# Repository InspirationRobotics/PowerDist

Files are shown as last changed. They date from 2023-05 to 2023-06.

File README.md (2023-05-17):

# PowerDist

`kicad` holds the kicad project / gerber files for the board, and `Power_dist` holds the code running on the microcontroller that actually does the 
hot-swapping.

The [BOM](https://docs.google.com/spreadsheets/d/1eEv6u52QYOC_kODey6bpNA8GYwr_zVqGhBdzeqPN1tI/edit?usp=sharing) holds all the internal component references 
that are in the kicad project i.e. component '1,1' is a 102k 0603 resistor. 

The [datasheet](https://docs.google.com/document/d/1oroizqdIsIZM1mA43HTIwGpKUFsHDlDQZaLfoY1nW0c/edit) for the board holds some useful information about the 
board capabilities and issues.

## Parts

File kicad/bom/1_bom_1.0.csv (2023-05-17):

Component | Description | Part | References | Value | Footprint | Quantity Per PCB | Datasheet | PN | Arrow Part Number | Arrow Price/Stock | Height | Manufacturer_Name | Manufacturer_Part_Number | Mouser Part Number | Mouser Price/Stock | Link
1 | Unpolarized capacitor | C | C3 C7 C29 C30 | 0.1uF | C_1608_603_B | 4 | ~
2 | Unpolarized capacitor | C | C2 C4 C8 | 1uF | C_1608_603_B | 3 | ~
3 | Unpolarized capacitor | C | C1 C14 C15 C16 C20 C21 C22 C26 C27 C28 | 10uF | C_1608_603_B | 10 | ~ | 100,000,013
4 | Unpolarized capacitor | C | C11 C12 C13 C17 C18 C19 C23 C24 C25 | 10uF | C_2012_805_B | 9 | ~ | 100,000,013
5 | Polarized capacitor | CP | C5 C6 C9 C10 | 470uF | THT_470uF_Cap | 4 | https://api.kemet.com/component-edge/download/datasheet/ESK477M025AH1AA.pdf
6 | Schottky diode | D_Schottky | D1 D2 | D_Schottky | D_SOD-323 | 2 | ~
7 | Light emitting diode | LED | D3 D4 D5 D6 D7 D8 D9 D10 | LED | R_1608_603_B | 8 | ~
8 | ARM Microcontrollers - MCU 256KB 32KB 48QFN GRN1.6-3.6V48MHz | ATSAMD21G18A-MUT | IC2 | ATSAMD21G18A-MUT | QFN50P700X700X90-49N-D | 1 | https://datasheet.datasheetarchive.com/originals/distributors/DKDS41/DSANUWW0026743.pdf |  | ATSAMD21G18A-MUT | https://www.arrow.com/en/products/atsamd21g18a-mut/microchip-technology?region=nac | 0.9 | Microchip | ATSAMD21G18A-MUT | 556-ATSAMD21G18A-MUT | https://www.mouser.co.uk/ProductDetail/Microchip-Technology-Atmel/ATSAMD21G18A-MUT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
9 |  | GD25Q16CWIGR | IC1 | GD25Q16CWIGR | PSON50P200X300X50-9N | 1 | https://ms.componentsearchengine.com/Datasheets/1/GD25Q16CWIGR.pdf |  |  |  | 0.8 | GigaDevice | GD25Q16CWIGR | 363-GD25Q16CWIGR | https://www.mouser.co.uk/ProductDetail/GigaDevice/GD25Q16CWIGR?qs=RcG8xmE7yp1dgxRTSLG3FQ%3D%3D
10 | USB Type A connector | USB_A | J2 | USB_A | amphenol_micro_usb_no_flange_10118192 | 1
11 |  | header_01x04 | J5 J6 | header_01x04 | Stemma_QT_2 | 2
12 |  | header_01x05 | J1 | header_01x05 | header_01x05_pitch2.54_tht | 1
13 | uSD Card connector | uSDCard | J7 | uSDCard | uSDCard_SD_503182_011 | 1 | x-devonthink-item://89382DC3-A8BA-4AFE-B050-E9E1112677D4
14 | Net tie, 4 pins | Net-Tie_4 | NT1 | Net-Tie_4 | NetTie-4_SMD_Pad2.0mm | 1 | ~
15 |  | CONN_1 | P1 P2 | CONN_1 | header_01x01_tht | 2
16 | NPN transistor, base/emitter/collector | BC847 | Q1 Q2 Q4 Q8 | BC847 | SOT-23 | 4 | ~ | 400,000,003
17 | N-MOSFET transistor, source/gate/drain | Q_NMOS_SGD | Q3 Q5 | PMOS_SGD | VDFN-8 | 2 | https://www.ti.com/lit/ds/symlink/csd25404q3.pdf?HQS=dis-dk-null-digikeymode-dsf-pf-null-wwe&ts=1673399419393
18 | Resistor | R | R38 R39 R40 R41 R42 R43 R44 R45 R46 R47 | 300 | R_1608_603_B | 10 | ~
19 | Resistor | R | R5 R9 R15 R16 | 470 | R_1608_603_B | 4 | ~
20 | Resistor | R | R8 R11 R22 R24 R51 R52 | 500 | R_2012_805_B | 6 | ~
21 | Resistor | R | R3 R4 R12 R13 R25 R26 R50 | 1k | R_1608_603_B | 7 | ~
22 | Resistor | R | R7 R10 R18 R20 R21 R23 | 4k7 | R_1608_603_B | 6 | ~
23 | Resistor | R | R1 R2 R6 R14 R48 R49 R53 | 10k | R_1608_603_B | 7 | ~ | 200,000,004
24 | Resistor | R | R17 R19 | 22k | R_1608_603_B | 2 | ~
25 | Resistor | R | R33 R35 R37 | 32.4k | R_1608_603_B | 3 | ~
26 | Resistor | R | R29 R30 R31 | 75k | R_1608_603_B | 3 | ~
27 | Resistor | R | R32 R34 R36 | 102k | R_1608_603_B | 3 | ~
28 |  | buzzer | SP1 SP2 | buzzer | 13-9mm_Buzzer | 2
29 | Push button switch, generic, two pins | SW_Push | SW1 | SW_Push | CK_PTS645_SMD | 1
30 |  | ACS781_1 | U2 U3 | ACS781 | 7-LR-PSOF | 2
31 |  | ARM-SWD-10 | U1 | ARM-SWD-10 | ARM-SWD-10 | 1 | http://suddendocs.samtec.com/catalog_english/ftsh_smt.pdf |  |  |  |  |  |  |  |  | https://www.digikey.com/en/products/detail/samtec-inc/FTSH-105-01-L-DV-K/1875039
32 |  | LM1085_2 | U10 U11 U12 | LM1085-3.0 | TO-263-3_TabPin2 | 3 | https://www.ti.com/general/docs/suppproductinfo.tsp?distId=10
33 |  | LM1085_1 | U7 U8 U9 | LM1085-5.0 | TO-263-3_TabPin2 | 3 | https://www.ti.com/lit/ds/symlink/lm1085.pdf?HQS=dis-dk-null-digikeymode-dsf-pf-null-wwe&ts=1674503286246
34 |  | MPM3610_1 | U4 U5 U6 | MPM3610 | 20-PowerLQFN | 3
35 |  | PCT2075 | U13 U14 | PCT2075 | PCT2075TP_147 | 2
36 |  | XT90PW-M | U15 U16 | XT90PW-M | AMASS_XT90PW-M_Horizontal | 2
37 |  | XT90PW-M | U17 U18 U19 U20 U21 U22 | XT90PW-M | AMASS_XT30U-F_1x02_P5.0mm_Vertical | 6
38 |  | XT90PW-M | U23 U24 U25 | XT90PW-M | AMASS_XT60-F_1x02_P7.20mm_Vertical | 3
Component Groups: | 38
Component Count: | 135
Fitted Components: | 135
Number of PCBs: | 1
Total components: | 135
Schematic Version: | 1.0
Schematic Date: | 2023-01-11
PCB Variant: | default
BoM Date: | Friday, January 27, 2023 at 11:06:49 AM
Schematic Source: | 1.0.kicad_sch
KiCad Version: | Eeschema (6.0.10-0)

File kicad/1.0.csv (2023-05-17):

Source: | /Users/seanboerhout/Documents/KiCAD/6.0/projects/Inspiration/Power_Dist/1.0/1.0.kicad_sch
Date: | Monday, January 23, 2023 at 03:24:27 PM
Tool: | Eeschema (6.0.10-0)
Generator: | /Applications/KiCad/KiCad.app/Contents/SharedSupport/plugins/bom_csv_grouped_by_value.py
Component Count: | 127
Individual Components:
Item | Qty | Reference(s) | Value | LibPart | Footprint | Datasheet | Arrow Part Number | Arrow Price/Stock | Description | Height | Link | Manufacturer_Name | Manufacturer_Part_Number | Mouser Part Number | Mouser Price/Stock | PN | Part
 |  | C1 | 10uF | 2.passive:C | 2_Passives_Capacitors_SMD_IPC:C_1608_603_B | ~ |  |  |  |  |  |  |  |  |  | 100,000,013
 |  | C2 | 1uF | 2.passive:C | 2_Passives_Capacitors_SMD_IPC:C_1608_603_B | ~ |  |  |  |  |  |  |  |  |  |  | 0603YC105KAT2A
 |  | C3 | 0.1uF | 2.passive:C | 2_Passives_Capacitors_SMD_IPC:C_1608_603_B | ~
 |  | C4 | 1uF | 2.passive:C | 2_Passives_Capacitors_SMD_IPC:C_1608_603_B | ~
 |  | C5 | 470uF | 2.passive:CP | 0_misc:THT_470uF_Cap | https://api.kemet.com/component-edge/download/datasheet/ESK477M025AH1AA.pdf
 |  | C6 | 470uF | 2.passive:CP | 0_misc:THT_470uF_Cap | https://api.kemet.com/component-edge/download/datasheet/ESK477M025AH1AA.pdf
 |  | C7 | 0.1uF | 2.passive:C | 2_Passives_Capacitors_SMD_IPC:C_1608_603_B | ~
 |  | C8 | 1uF | 2.passive:C | 2_Passives_Capacitors_SMD_IPC:C_1608_603_B | ~
 |  | C9 | 470uF | 2.passive:CP | 0_misc:THT_470uF_Cap | https://api.kemet.com/component-edge/download/datasheet/ESK477M025AH1AA.pdf
 |  | C10 | 470uF | 2.passive:CP | 0_misc:THT_470uF_Cap | https://api.kemet.com/component-edge/download/datasheet/ESK477M025AH1AA.pdf
 |  | C11 | 10uF | 2.passive:C | 2_Passives_Capacitors_SMD_IPC:C_2012_805_B | ~ |  |  |  |  |  |  |  |  |  | 100,000,013
 |  | C12 | 10uF | 2.passive:C | 2_Passives_Capacitors_SMD_IPC:C_2012_805_B | ~ |  |  |  |  |  |  |  |  |  | 100,000,013
 |  | C13 | 10uF | 2.passive:C | 2_Passives_Capacitors_SMD_IPC:C_2012_805_B | ~ |  |  |  |  |  |  |  |  |  | 100,000,013
 |  | C14 | 10uF | 2.passive:C | 2_Passives_Capacitors_SMD_IPC:C_1608_603_B | ~ |  |  |  |  |  |  |  |  |  | 100,000,013
 |  | C15 | 10uF | 2.passive:C | 2_Passives_Capacitors_SMD_IPC:C_1608_603_B | ~ |  |  |  |  |  |  |  |  |  | 100,000,013
 |  | C16 | 10uF | 2.passive:C | 2_Passives_Capacitors_SMD_IPC:C_1608_603_B | ~ |  |  |  |  |  |  |  |  |  | 100,000,013
 |  | C17 | 10uF | 2.passive:C | 2_Passives_Capacitors_SMD_IPC:C_2012_805_B | ~ |  |  |  |  |  |  |  |  |  | 100,000,013
 |  | C18 | 10uF | 2.passive:C | 2_Passives_Capacitors_SMD_IPC:C_2012_805_B | ~ |  |  |  |  |  |  |  |  |  | 100,000,013
 |  | C19 | 10uF | 2.passive:C | 2_Passives_Capacitors_SMD_IPC:C_2012_805_B | ~ |  |  |  |  |  |  |  |  |  | 100,000,013
 |  | C20 | 10uF | 2.passive:C | 2_Passives_Capacitors_SMD_IPC:C_1608_603_B | ~ |  |  |  |  |  |  |  |  |  | 100,000,013
 |  | C21 | 10uF | 2.passive:C | 2_Passives_Capacitors_SMD_IPC:C_1608_603_B | ~ |  |  |  |  |  |  |  |  |  | 100,000,013
 |  | C22 | 10uF | 2.passive:C | 2_Passives_Capacitors_SMD_IPC:C_1608_603_B | ~ |  |  |  |  |  |  |  |  |  | 100,000,013
 |  | C23 | 10uF | 2.passive:C | 2_Passives_Capacitors_SMD_IPC:C_2012_805_B | ~ |  |  |  |  |  |  |  |  |  | 100,000,013
 |  | C24 | 10uF | 2.passive:C | 2_Passives_Capacitors_SMD_IPC:C_2012_805_B | ~ |  |  |  |  |  |  |  |  |  | 100,000,013
 |  | C25 | 10uF | 2.passive:C | 2_Passives_Capacitors_SMD_IPC:C_2012_805_B | ~ |  |  |  |  |  |  |  |  |  | 100,000,013
 |  | C26 | 10uF | 2.passive:C | 2_Passives_Capacitors_SMD_IPC:C_1608_603_B | ~ |  |  |  |  |  |  |  |  |  | 100,000,013
 |  | C27 | 10uF | 2.passive:C | 2_Passives_Capacitors_SMD_IPC:C_1608_603_B | ~ |  |  |  |  |  |  |  |  |  | 100,000,013
 |  | C28 | 10uF | 2.passive:C | 2_Passives_Capacitors_SMD_IPC:C_1608_603_B | ~ |  |  |  |  |  |  |  |  |  | 100,000,013
 |  | C29 | 0.1uF | 2.passive:C | 2_Passives_Capacitors_SMD_IPC:C_1608_603_B | ~
 |  | C30 | 0.1uF | 2.passive:C | 2_Passives_Capacitors_SMD_IPC:C_1608_603_B | ~
 |  | D1 | D_Schottky | 1.semi.discrete:D_Schottky | 1_Semi_Discrete_Diodes_SMD:D_SOD-323 | ~
 |  | D2 | D_Schottky | 1.semi.discrete:D_Schottky | 1_Semi_Discrete_Diodes_SMD:D_SOD-323 | ~
 |  | D3 | LED | 1.semi.opto:LED | 2_Passives_Resistors_SMD_IPC:R_1608_603_B | ~
 |  | D4 | LED | 1.semi.opto:LED | 2_Passives_Resistors_SMD_IPC:R_1608_603_B | ~
 |  | D5 | LED | 1.semi.opto:LED | 2_Passives_Resistors_SMD_IPC:R_1608_603_B | ~
 |  | D6 | LED | 1.semi.opto:LED | 2_Passives_Resistors_SMD_IPC:R_1608_603_B | ~
 |  | D7 | LED | 1.semi.opto:LED | 2_Passives_Resistors_SMD_IPC:R_1608_603_B | ~
 |  | D8 | LED | 1.semi.opto:LED | 2_Passives_Resistors_SMD_IPC:R_1608_603_B | ~
 |  | D9 | LED | 1.semi.opto:LED | 2_Passives_Resistors_SMD_IPC:R_1608_603_B | ~
 |  | D10 | LED | 1.semi.opto:LED | 2_Passives_Resistors_SMD_IPC:R_1608_603_B | ~
 |  | IC1 | GD25Q16CWIGR | 1.semi.embedded:GD25Q16CWIGR | 1_Semi_Misc:PSON50P200X300X50-9N | https://ms.componentsearchengine.com/Datasheets/1/GD25Q16CWIGR.pdf |  |  | NOR Flash 16Mbit NOR Flash /3.3V /WSON8 6*5mm /Industrial(-40 to +85 ) /T&R | 0.8 |  | GigaDevice | GD25Q16CWIGR | 363-GD25Q16CWIGR | https://www.mouser.co.uk/ProductDetail/GigaDevice/GD25Q16CWIGR?qs=RcG8xmE7yp1dgxRTSLG3FQ%3D%3D
 |  | IC2 | ATSAMD21G18A-MUT | 1.semi.embedded_samdx:ATSAMD21G18A-MUT | 1_Semi_QFN:QFN50P700X700X90-49N-D | https://datasheet.datasheetarchive.com/originals/distributors/DKDS41/DSANUWW0026743.pdf | ATSAMD21G18A-MUT | https://www.arrow.com/en/products/atsamd21g18a-mut/microchip-technology?region=nac | ARM Microcontrollers - MCU 256KB 32KB 48QFN GRN1.6-3.6V48MHz | 0.9 |  | Microchip | ATSAMD21G18A-MUT | 556-ATSAMD21G18A-MUT | https://www.mouser.co.uk/ProductDetail/Microchip-Technology-Atmel/ATSAMD21G18A-MUT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
 |  | J1 | header_01x05 | 5.connector.interconnect:header_01x05 | 5_Connectors_misc:header_01x05_pitch2.54_tht
 |  | J2 | USB_A | 5.connector.interconnect.usb_dvi_hdmi:USB_A | 5_Connectors_misc:amphenol_micro_usb_no_flange_10118192
 |  | J5 | header_01x04 | 5.connector.interconnect:header_01x04 | 5_Connectors_misc:Stemma_QT_2
 |  | J6 | header_01x04 | 5.connector.interconnect:header_01x04 | 5_Connectors_misc:Stemma_QT_2
 |  | J7 | uSDCard | 5.connector.interconnect.usb_dvi_hdmi:uSDCard | 5_Connectors_Molex:uSDCard_SD_503182_011 | x-devonthink-item://89382DC3-A8BA-4AFE-B050-E9E1112677D4
 |  | NT1 | Net-Tie_4 | 2.passive:Net-Tie_4 | 0_NetTie:NetTie-4_SMD_Pad2.0mm | ~
 |  | P1 | CONN_1 | 5.connector.interconnect:CONN_1 | 5_Connectors_misc:header_01x01_tht
 |  | P2 | CONN_1 | 5.connector.interconnect:CONN_1 | 5_Connectors_misc:header_01x01_tht
 |  | Q1 | BC847 | 1.semi.discrete:BC847 | 1_Semi_TO_SOT:SOT-23 | ~ |  |  |  |  |  |  |  |  |  | 400,000,003
 |  | Q2 | BC847 | 1.semi.discrete:BC847 | 1_Semi_TO_SOT:SOT-23 | ~ |  |  |  |  |  |  |  |  |  | 400,000,003
 |  | Q3 | PMOS_SGD | 1.semi.discrete:Q_NMOS_SGD | 1_Semi_TO_SOT:VDFN-8 | https://www.ti.com/lit/ds/symlink/csd25404q3.pdf?HQS=dis-dk-null-digikeymode-dsf-pf-null-wwe&ts=1673399419393
 |  | Q4 | BC847 | 1.semi.discrete:BC847 | 1_Semi_TO_SOT:SOT-23 | ~ |  |  |  |  |  |  |  |  |  | 400,000,003
 |  | Q5 | PMOS_SGD | 1.semi.discrete:Q_NMOS_SGD | 1_Semi_TO_SOT:VDFN-8 | https://www.ti.com/lit/ds/symlink/csd25404q3.pdf?HQS=dis-dk-null-digikeymode-dsf-pf-null-wwe&ts=1673399419393
 |  | Q8 | BC847 | 1.semi.discrete:BC847 | 1_Semi_TO_SOT:SOT-23 | ~ |  |  |  |  |  |  |  |  |  | 400,000,003
 |  | R1 | 10k | 2.passive:R | 2_Passives_Resistors_SMD_IPC:R_1608_603_B | ~ |  |  |  |  |  |  |  |  |  | 200,000,004
 |  | R2 | 10k | 2.passive:R | 2_Passives_Resistors_SMD_IPC:R_1608_603_B | ~
 |  | R3 | 1k | 2.passive:R | 2_Passives_Resistors_SMD_IPC:R_1608_603_B | ~
 |  | R4 | 1k | 2.passive:R | 2_Passives_Resistors_SMD_IPC:R_1608_603_B | ~
 |  | R5 | 470 | 2.passive:R | 2_Passives_Resistors_SMD_IPC:R_1608_603_B | ~
 |  | R6 | 10k | 2.passive:R | 2_Passives_Resistors_SMD_IPC:R_1608_603_B | ~
 |  | R7 | 4k7 | 2.passive:R | 2_Passives_Resistors_SMD_IPC:R_1608_603_B | ~
 |  | R8 | 500 | 2.passive:R | 2_Passives_Resistors_SMD_IPC:R_2012_805_B | ~
 |  | R9 | 470 | 2.passive:R | 2_Passives_Resistors_SMD_IPC:R_1608_603_B | ~
 |  | R10 | 4k7 | 2.passive:R | 2_Passives_Resistors_SMD_IPC:R_1608_603_B | ~
 |  | R11 | 500 | 2.passive:R | 2_Passives_Resistors_SMD_IPC:R_2012_805_B | ~
 |  | R12 | 1k | 2.passive:R | 2_Passives_Resistors_SMD_IPC:R_1608_603_B | ~
 |  | R13 | 1k | 2.passive:R | 2_Passives_Resistors_SMD_IPC:R_1608_603_B | ~
 |  | R14 | 10k | 2.passive:R | 2_Passives_Resistors_SMD_IPC:R_1608_603_B | ~
 |  | R15 | 470 | 2.passive:R | 2_Passives_Resistors_SMD_IPC:R_1608_603_B | ~
 |  | R16 | 470 | 2.passive:R | 2_Passives_Resistors_SMD_IPC:R_1608_603_B | ~
 |  | R17 | 22k | 2.passive:R | 2_Passives_Resistors_SMD_IPC:R_1608_603_B | ~
 |  | R18 | 4k7 | 2.passive:R | 2_Passives_Resistors_SMD_IPC:R_1608_603_B | ~
 |  | R19 | 22k | 2.passive:R | 2_Passives_Resistors_SMD_IPC:R_1608_603_B | ~
 |  | R20 | 4k7 | 2.passive:R | 2_Passives_Resistors_SMD_IPC:R_1608_603_B | ~
 |  | R21 | 4k7 | 2.passive:R | 2_Passives_Resistors_SMD_IPC:R_1608_603_B | ~
 |  | R22 | 500 | 2.passive:R | 2_Passives_Resistors_SMD_IPC:R_2012_805_B | ~
 |  | R23 | 4k7 | 2.passive:R | 2_Passives_Resistors_SMD_IPC:R_1608_603_B | ~
 |  | R24 | 500 | 2.passive:R | 2_Passives_Resistors_SMD_IPC:R_2012_805_B | ~
 |  | R25 | 1k | 2.passive:R | 2_Passives_Resistors_SMD_IPC:R_1608_603_B | ~
 |  | R26 | 1k | 2.passive:R | 2_Passives_Resistors_SMD_IPC:R_1608_603_B | ~
 |  | R29 | 75k | 2.passive:R | 2_Passives_Resistors_SMD_IPC:R_1608_603_B | ~
 |  | R30 | 75k | 2.passive:R | 2_Passives_Resistors_SMD_IPC:R_1608_603_B | ~
 |  | R31 | 75k | 2.passive:R | 2_Passives_Resistors_SMD_IPC:R_1608_603_B | ~
 |  | R32 | 102k | 2.passive:R | 2_Passives_Resistors_SMD_IPC:R_1608_603_B | ~
 |  | R33 | 32.4k | 2.passive:R | 2_Passives_Resistors_SMD_IPC:R_1608_603_B | ~
 |  | R34 | 102k | 2.passive:R | 2_Passives_Resistors_SMD_IPC:R_1608_603_B | ~
 |  | R35 | 32.4k | 2.passive:R | 2_Passives_Resistors_SMD_IPC:R_1608_603_B | ~
 |  | R36 | 102k | 2.passive:R | 2_Passives_Resistors_SMD_IPC:R_1608_603_B | ~
 |  | R37 | 32.4k | 2.passive:R | 2_Passives_Resistors_SMD_IPC:R_1608_603_B | ~
 |  | R38 | 300 | 2.passive:R | 2_Passives_Resistors_SMD_IPC:R_1608_603_B | ~
 |  | R39 | 300 | 2.passive:R | 2_Passives_Resistors_SMD_IPC:R_1608_603_B | ~
 |  | R40 | 300 | 2.passive:R | 2_Passives_Resistors_SMD_IPC:R_1608_603_B | ~
 |  | R41 | 300 | 2.passive:R | 2_Passives_Resistors_SMD_IPC:R_1608_603_B | ~
 |  | R42 | 300 | 2.passive:R | 2_Passives_Resistors_SMD_IPC:R_1608_603_B | ~
 |  | R43 | 300 | 2.passive:R | 2_Passives_Resistors_SMD_IPC:R_1608_603_B | ~
 |  | R44 | 300 | 2.passive:R | 2_Passives_Resistors_SMD_IPC:R_1608_603_B | ~
 |  | R45 | 300 | 2.passive:R | 2_Passives_Resistors_SMD_IPC:R_1608_603_B | ~
 |  | R46 | 300 | 2.passive:R | 2_Passives_Resistors_SMD_IPC:R_1608_603_B | ~
 |  | R47 | 300 | 2.passive:R | 2_Passives_Resistors_SMD_IPC:R_1608_603_B | ~
 |  | R48 | 10k | 2.passive:R | 2_Passives_Resistors_SMD_IPC:R_1608_603_B | ~
 |  | R49 | 10k | 2.passive:R | 2_Passives_Resistors_SMD_IPC:R_1608_603_B | ~
 |  | R50 | 1k | 2.passive:R | 2_Passives_Resistors_SMD_IPC:R_1608_603_B | ~
 |  | R51 | 500 | 2.passive:R | 2_Passives_Resistors_SMD_IPC:R_2012_805_B | ~
 |  | R52 | 500 | 2.passive:R | 2_Passives_Resistors_SMD_IPC:R_2012_805_B | ~
 |  | R53 | 10k | 2.passive:R | 2_Passives_Resistors_SMD_IPC:R_1608_603_B | ~
 |  | SP1 | buzzer | 3.electromechanical.audio:buzzer | 3_Electromechanical_Audio:13-9mm_Buzzer
 |  | SP2 | buzzer | 3.electromechanical.audio:buzzer | 3_Electromechanical_Audio:13-9mm_Buzzer
 |  | SW1 | SW_Push | 3.electromechanical.switch:SW_Push | 3_Electromechanical_Buttons_Switches_SMD:CK_PTS645_SMD
 |  | TP1 | TEST | 5.connector.interconnect:TEST | 0_misc:test_point_1.0mm_square
 |  | U1 | ARM-SWD-10 | 5.connector.interconnect.usb_dvi_hdmi:ARM-SWD-10 | 5_Connectors_misc:ARM-SWD-10 | http://suddendocs.samtec.com/catalog_english/ftsh_smt.pdf |  |  |  |  | https://www.digikey.com/en/products/detail/samtec-inc/FTSH-105-01-L-DV-K/1875039
 |  | U2 | ACS781 | :ACS781_1 | 1_Semi_TO_SOT:7-LR-PSOF
 |  | U3 | ACS781 | :ACS781_1 | 1_Semi_TO_SOT:7-LR-PSOF
 |  | U4 | MPM3610 | :MPM3610_1 | 1_Semi_QFN:20-PowerLQFN
 |  | U5 | MPM3610 | :MPM3610_1 | 1_Semi_QFN:20-PowerLQFN
 |  | U6 | MPM3610 | :MPM3610_1 | 1_Semi_QFN:20-PowerLQFN
 |  | U7 | LM1085-5.0 | :LM1085_1 | 1_Semi_TO_SOT:TO-263-3_TabPin2 | https://www.ti.com/lit/ds/symlink/lm1085.pdf?HQS=dis-dk-null-digikeymode-dsf-pf-null-wwe&ts=1674503286246
 |  | U8 | LM1085-5.0 | :LM1085_1 | 1_Semi_TO_SOT:TO-263-3_TabPin2 | https://www.ti.com/lit/ds/symlink/lm1085.pdf?HQS=dis-dk-null-digikeymode-dsf-pf-null-wwe&ts=1674503286246
 |  | U9 | LM1085-5.0 | :LM1085_1 | 1_Semi_TO_SOT:TO-263-3_TabPin2 | https://www.ti.com/lit/ds/symlink/lm1085.pdf?HQS=dis-dk-null-digikeymode-dsf-pf-null-wwe&ts=1674503286246
 |  | U10 | LM1085-3.0 | :LM1085_2 | 1_Semi_TO_SOT:TO-263-3_TabPin2 | https://www.ti.com/general/docs/suppproductinfo.tsp?distId=10
 |  | U11 | LM1085-3.0 | :LM1085_2 | 1_Semi_TO_SOT:TO-263-3_TabPin2 | https://www.ti.com/general/docs/suppproductinfo.tsp?distId=10
 |  | U12 | LM1085-3.0 | :LM1085_2 | 1_Semi_TO_SOT:TO-263-3_TabPin2 | https://www.ti.com/general/docs/suppproductinfo.tsp?distId=10
 |  | U13 | PCT2075 | 1.semi.ic.sensor:PCT2075 | 1_Semi_Misc:PCT2075TP_147
 |  | U14 | PCT2075 | 1.semi.ic.sensor:PCT2075 | 1_Semi_Misc:PCT2075TP_147
 |  | U15 | XT90PW-M | :XT90PW-M_1 | 5_Connectors_misc:AMASS_XT90PW-M_Horizontal
 |  | U16 | XT90PW-M | 5.connector.interconnect:XT90PW-M | 5_Connectors_misc:AMASS_XT90PW-M_Horizontal
Collated Components:
Item | Qty | Reference(s) | Value | LibPart | Footprint | Datasheet | Arrow Part Number | Arrow Price/Stock | Description | Height | Link | Manufacturer_Name | Manufacturer_Part_Number | Mouser Part Number | Mouser Price/Stock | PN | Part
1 | 10 | C1, C14, C15, C16, C20, C21, C22, C26, C27, C28 | 10uF | 2.passive:C | 2_Passives_Capacitors_SMD_IPC:C_1608_603_B | ~ |  |  |  |  |  |  |  |  |  | 100,000,013
2 | 3 | C2, C4, C8 | 1uF | 2.passive:C | 2_Passives_Capacitors_SMD_IPC:C_1608_603_B | ~ |  |  |  |  |  |  |  |  |  |  | 0603YC105KAT2A
3 | 4 | C3, C7, C29, C30 | 0.1uF | 2.passive:C | 2_Passives_Capacitors_SMD_IPC:C_1608_603_B | ~
4 | 4 | C5, C6, C9, C10 | 470uF | 2.passive:CP | 0_misc:THT_470uF_Cap | https://api.kemet.com/component-edge/download/datasheet/ESK477M025AH1AA.pdf
5 | 9 | C11, C12, C13, C17, C18, C19, C23, C24, C25 | 10uF | 2.passive:C | 2_Passives_Capacitors_SMD_IPC:C_2012_805_B | ~ |  |  |  |  |  |  |  |  |  | 100,000,013
6 | 2 | D1, D2 | D_Schottky | 1.semi.discrete:D_Schottky | 1_Semi_Discrete_Diodes_SMD:D_SOD-323 | ~
7 | 8 | D3, D4, D5, D6, D7, D8, D9, D10 | LED | 1.semi.opto:LED | 2_Passives_Resistors_SMD_IPC:R_1608_603_B | ~
8 | 1 | IC1 | GD25Q16CWIGR | 1.semi.embedded:GD25Q16CWIGR | 1_Semi_Misc:PSON50P200X300X50-9N | https://ms.componentsearchengine.com/Datasheets/1/GD25Q16CWIGR.pdf |  |  | NOR Flash 16Mbit NOR Flash /3.3V /WSON8 6*5mm /Industrial(-40 to +85 ) /T&R | 0.8 |  | GigaDevice | GD25Q16CWIGR | 363-GD25Q16CWIGR | https://www.mouser.co.uk/ProductDetail/GigaDevice/GD25Q16CWIGR?qs=RcG8xmE7yp1dgxRTSLG3FQ%3D%3D
9 | 1 | IC2 | ATSAMD21G18A-MUT | 1.semi.embedded_samdx:ATSAMD21G18A-MUT | 1_Semi_QFN:QFN50P700X700X90-49N-D | https://datasheet.datasheetarchive.com/originals/distributors/DKDS41/DSANUWW0026743.pdf | ATSAMD21G18A-MUT | https://www.arrow.com/en/products/atsamd21g18a-mut/microchip-technology?region=nac | ARM Microcontrollers - MCU 256KB 32KB 48QFN GRN1.6-3.6V48MHz | 0.9 |  | Microchip | ATSAMD21G18A-MUT | 556-ATSAMD21G18A-MUT | https://www.mouser.co.uk/ProductDetail/Microchip-Technology-Atmel/ATSAMD21G18A-MUT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
10 | 1 | J1 | header_01x05 | 5.connector.interconnect:header_01x05 | 5_Connectors_misc:header_01x05_pitch2.54_tht
11 | 1 | J2 | USB_A | 5.connector.interconnect.usb_dvi_hdmi:USB_A | 5_Connectors_misc:amphenol_micro_usb_no_flange_10118192
12 | 2 | J5, J6 | header_01x04 | 5.connector.interconnect:header_01x04 | 5_Connectors_misc:Stemma_QT_2
13 | 1 | J7 | uSDCard | 5.connector.interconnect.usb_dvi_hdmi:uSDCard | 5_Connectors_Molex:uSDCard_SD_503182_011 | x-devonthink-item://89382DC3-A8BA-4AFE-B050-E9E1112677D4
14 | 1 | NT1 | Net-Tie_4 | 2.passive:Net-Tie_4 | 0_NetTie:NetTie-4_SMD_Pad2.0mm | ~
15 | 2 | P1, P2 | CONN_1 | 5.connector.interconnect:CONN_1 | 5_Connectors_misc:header_01x01_tht
16 | 4 | Q1, Q2, Q4, Q8 | BC847 | 1.semi.discrete:BC847 | 1_Semi_TO_SOT:SOT-23 | ~ |  |  |  |  |  |  |  |  |  | 400,000,003
17 | 2 | Q3, Q5 | PMOS_SGD | 1.semi.discrete:Q_NMOS_SGD | 1_Semi_TO_SOT:VDFN-8 | https://www.ti.com/lit/ds/symlink/csd25404q3.pdf?HQS=dis-dk-null-digikeymode-dsf-pf-null-wwe&ts=1673399419393
18 | 7 | R1, R2, R6, R14, R48, R49, R53 | 10k | 2.passive:R | 2_Passives_Resistors_SMD_IPC:R_1608_603_B | ~ |  |  |  |  |  |  |  |  |  | 200,000,004
19 | 7 | R3, R4, R12, R13, R25, R26, R50 | 1k | 2.passive:R | 2_Passives_Resistors_SMD_IPC:R_1608_603_B | ~
20 | 4 | R5, R9, R15, R16 | 470 | 2.passive:R | 2_Passives_Resistors_SMD_IPC:R_1608_603_B | ~
21 | 6 | R7, R10, R18, R20, R21, R23 | 4k7 | 2.passive:R | 2_Passives_Resistors_SMD_IPC:R_1608_603_B | ~
22 | 6 | R8, R11, R22, R24, R51, R52 | 500 | 2.passive:R | 2_Passives_Resistors_SMD_IPC:R_2012_805_B | ~
23 | 2 | R17, R19 | 22k | 2.passive:R | 2_Passives_Resistors_SMD_IPC:R_1608_603_B | ~
24 | 3 | R29, R30, R31 | 75k | 2.passive:R | 2_Passives_Resistors_SMD_IPC:R_1608_603_B | ~
25 | 3 | R32, R34, R36 | 102k | 2.passive:R | 2_Passives_Resistors_SMD_IPC:R_1608_603_B | ~
26 | 3 | R33, R35, R37 | 32.4k | 2.passive:R | 2_Passives_Resistors_SMD_IPC:R_1608_603_B | ~
27 | 10 | R38, R39, R40, R41, R42, R43, R44, R45, R46, R47 | 300 | 2.passive:R | 2_Passives_Resistors_SMD_IPC:R_1608_603_B | ~
28 | 2 | SP1, SP2 | buzzer | 3.electromechanical.audio:buzzer | 3_Electromechanical_Audio:13-9mm_Buzzer
29 | 1 | SW1 | SW_Push | 3.electromechanical.switch:SW_Push | 3_Electromechanical_Buttons_Switches_SMD:CK_PTS645_SMD
30 | 1 | TP1 | TEST | 5.connector.interconnect:TEST | 0_misc:test_point_1.0mm_square
31 | 1 | U1 | ARM-SWD-10 | 5.connector.interconnect.usb_dvi_hdmi:ARM-SWD-10 | 5_Connectors_misc:ARM-SWD-10 | http://suddendocs.samtec.com/catalog_english/ftsh_smt.pdf |  |  |  |  | https://www.digikey.com/en/products/detail/samtec-inc/FTSH-105-01-L-DV-K/1875039
32 | 2 | U2, U3 | ACS781 | :ACS781_1 | 1_Semi_TO_SOT:7-LR-PSOF
33 | 3 | U4, U5, U6 | MPM3610 | :MPM3610_1 | 1_Semi_QFN:20-PowerLQFN
34 | 3 | U7, U8, U9 | LM1085-5.0 | :LM1085_1 | 1_Semi_TO_SOT:TO-263-3_TabPin2 | https://www.ti.com/lit/ds/symlink/lm1085.pdf?HQS=dis-dk-null-digikeymode-dsf-pf-null-wwe&ts=1674503286246
35 | 3 | U10, U11, U12 | LM1085-3.0 | :LM1085_2 | 1_Semi_TO_SOT:TO-263-3_TabPin2 | https://www.ti.com/general/docs/suppproductinfo.tsp?distId=10
36 | 2 | U13, U14 | PCT2075 | 1.semi.ic.sensor:PCT2075 | 1_Semi_Misc:PCT2075TP_147
37 | 1 | U15 | XT90PW-M | :XT90PW-M_1 | 5_Connectors_misc:AMASS_XT90PW-M_Horizontal
38 | 1 | U16 | XT90PW-M | 5.connector.interconnect:XT90PW-M | 5_Connectors_misc:AMASS_XT90PW-M_Horizontal

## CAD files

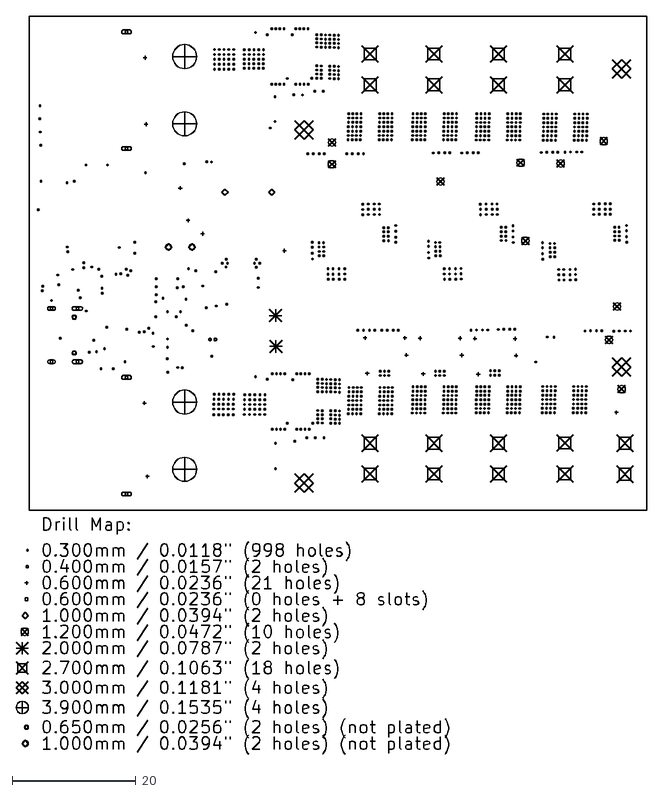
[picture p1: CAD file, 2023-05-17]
kicad/gerbers/1.0-drl_map.dxf
102.1 x 119.5

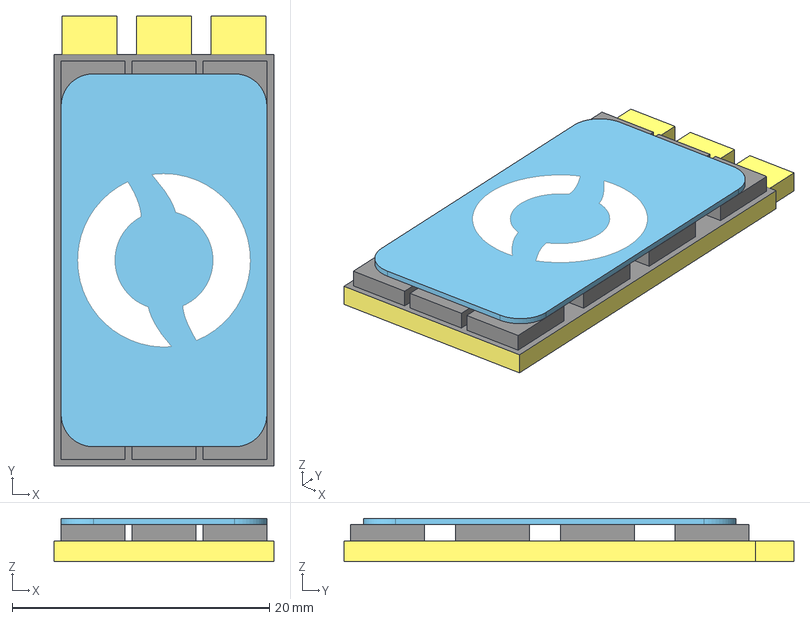
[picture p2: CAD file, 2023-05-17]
kicad/hot_swap_3dmodels/BESC30-R3.step
17.1 x 35.0 x 3.35 mm
BASICESC-G-PCB-X1
BASICESC-E-MOSFET x 12
BASICESC-M-HEAT-SPREADER-X1

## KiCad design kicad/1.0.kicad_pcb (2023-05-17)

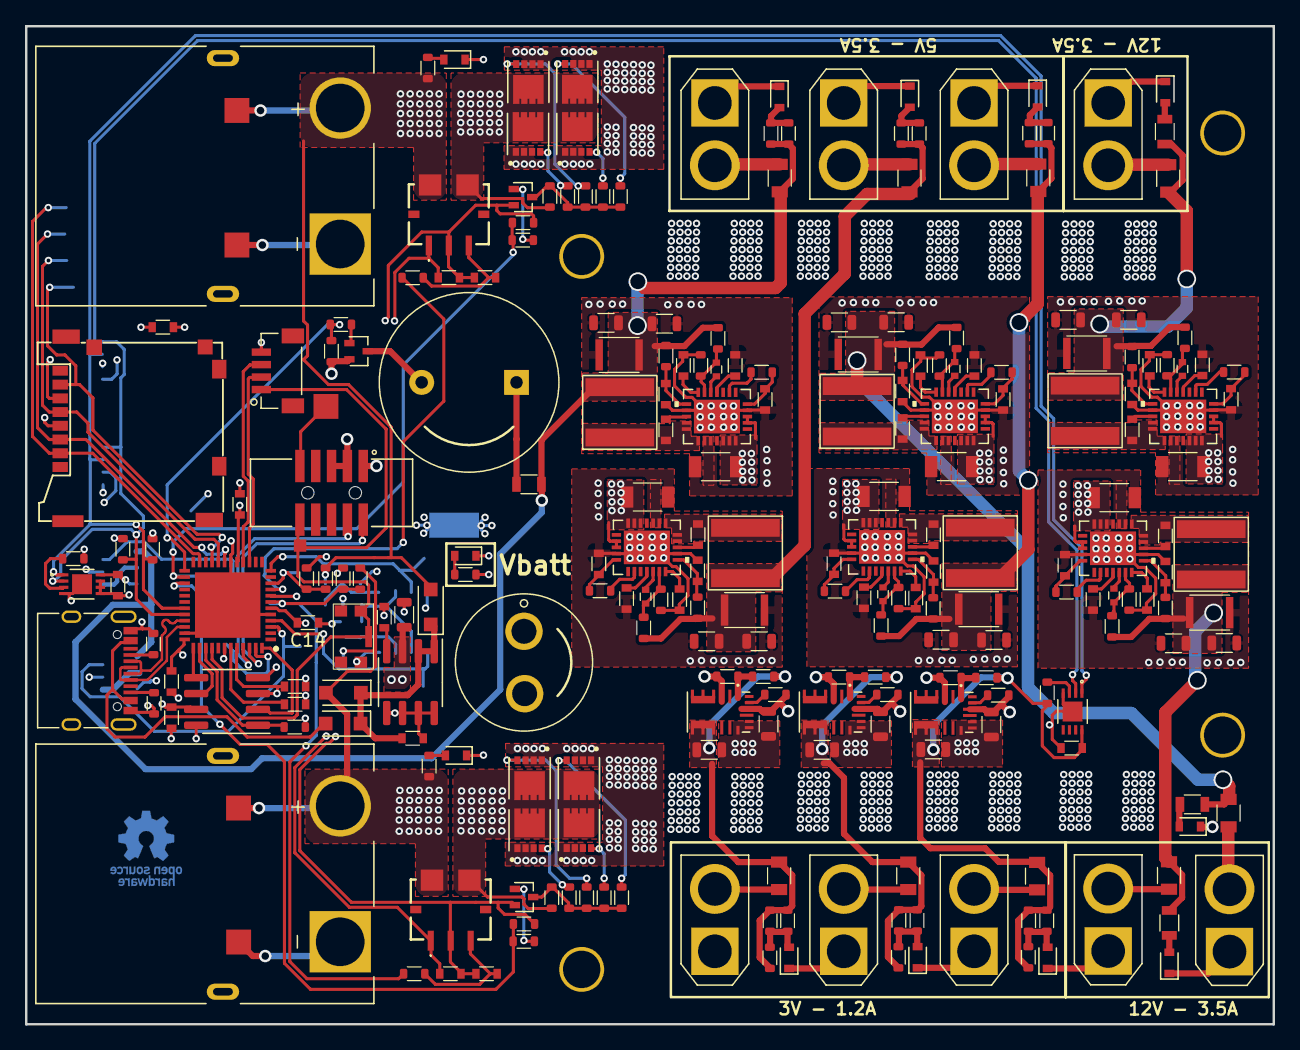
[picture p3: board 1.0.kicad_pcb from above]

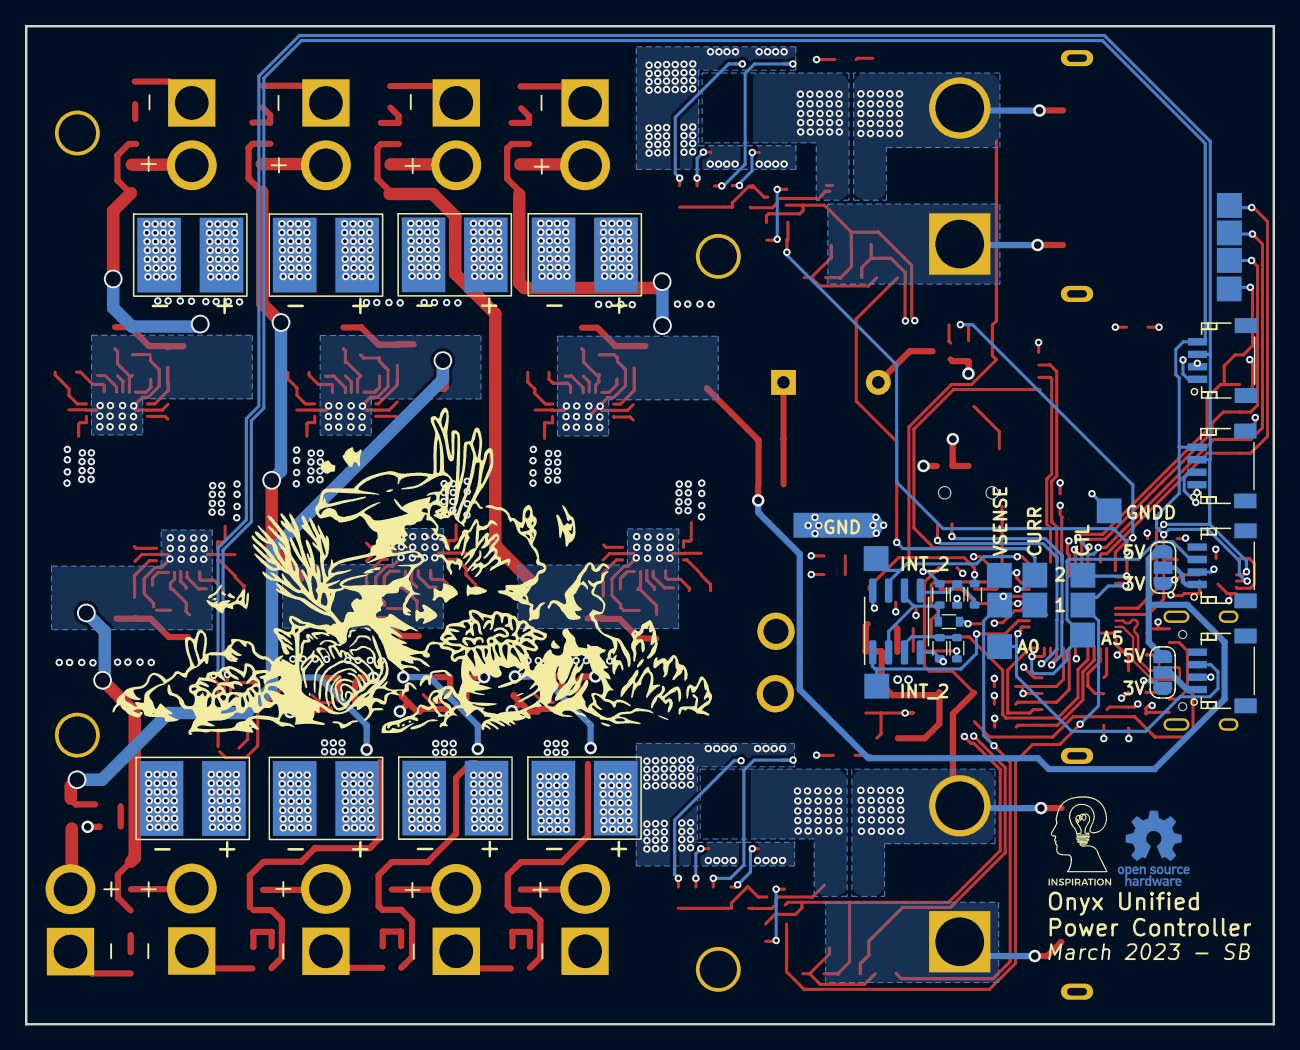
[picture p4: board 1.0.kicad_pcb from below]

Board: 4 copper layers, 100.0 x 80.0 mm, 290 parts (39 on the bottom side), 157 nets.

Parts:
C1, C3, C7, C9, C10, C14, C17, C29, C30, C32, C35, C37, C38, C41, C43, C65, C66, C67, C68, C69, C72, C81: 0.1u; C_1608_603_B
C2, C4, C8, C33: 1u; C_1608_603_B
C5: 470u; THT_470uF_Cap
C6, C21, C42, C47, C52, C58: 22u; C_3225_1210_B
C11, C12, C13, C15, C16, C20, C22, C26, C48, C50, C51, C56, C57, C74, C75, C80: 10u; C_2012_805_B
C18, C19, C24, C53, C54, C55: 4u7; C_3216_1206_A
C23, C25, C28, C59, C60, C61: 2u2; C_1608_603_B
C27, C31, C36, C62, C63, C64: 5n6; C_1608_603_B
C34: 100p; C_1608_603_B
C39, C40, C45, C70, C71, C73: OPEN; C_1005_402_A
C44, C46, C49: 47u; C_2012_805_B
D1, D2, D12: D_Schottky; D_SOD-123F
D3, D4, D5, D6, D7, D8, D9, D10, D11, D14, D15, D16: LED; D_0603
F1, F2, F3, F4, F5, F6, F7, F8, F9: Polyfuse_Small; R_2012_805_A
IC1: GD25Q16CWIGR; SOIC-8_3.9x4.9mm_P1.27mm
IC2: ATSAMD21G18A-MUT; QFN50P700X700X90-49N-D
J1: header_01x04; Stemma_QT_V
J3, J4, J5, J6: header_01x04; Stemma_QT_2
J7: uSDCard; uSDCard_SD_503182_011
JP1, JP2: Jumper_NO_Dual; SolderJumper-3_P1.3mm_Open_RoundedPad1.0x1.5mm_NumberLabels
L1, L2, L3: 6u8; XGL6060
L4, L5, L6: 15u; XGL6060
NT1: net-tie; NetTie-2_SMD_Pad2.0mm
P7: CONN_1; OSHW-Logo_5.7x6mm_Copper
Q1, Q2, Q7: Q_NMOS_GSD; SOT-323FL
Q3, Q4, Q5, Q6, Q9, Q10, Q11, Q12: PMOS_SGD; VDFN-8
R1, R2, R4, R6, R23, R48, R49, R53, R67, R80, R82, R84, R90, R92, R94: 10k; R_1608_603_B
R3, R52, R73, R81, R83, R85, R99: 40k2; C_1608_603_B
R5, R9, R15: 470; R_1608_603_B
R7, R18, R20, R24, R26, R50, R97, R98: 4k7; R_1608_603_B
R8, R10: 5k1; R_1608_603_B
R11, R27, R74, R77, R79, R96: 28k; R_1608_603_B
R12, R13, R14, R21, R22, R28, R54, R55, R56, R57: 1k; R_1608_603_B
R16, R25, R38, R39, R40, R41, R42, R43, R44, R45, R46, R47, R58, R59, R60, R61, R62, R63: 300; R_1608_603_B
R17, R19: 22k; R_1608_603_B
R29, R30, R31: 75k; R_1608_603_B
R32, R34, R36: 102k; R_1608_603_B
R33, R35, R37: 32.4k; R_1608_603_B
R51, R68, R69, R70: 500; R_2012_805_B
R66, R71, R75, R86, R87, R88: 4.7; R_1608_603_B
R72, R76, R78: 127k; R_1608_603_B
R89, R91, R93: 124k; R_1608_603_B
SP1: buzzer; 13-9mm_Buzzer
SW1: SW_Push; KMR243GLFG
TP1: TEST; test_point_1.0mm_square
TP2, TP3, TP4, TP5, TP6, TP7, TP8, TP9, TP10, TP11, TP12, TP13, TP14, TP15, TP16, TP17, TP18, TP19, TP20, TP21, TP22: TEST; test_point_2mm_square
U1: ARM-SWD-10
U2, U3: ACS781; 7-LR-PSOF
U4, U5, U6: MPM3610; 20-PowerLQFN
U7, U8, U27, U28: Mounting-holes; plated_hole_3.0x3.6mm
U9, U11, U12, U29, U30, U31: MAX17573; 24_WFQFN
U10: USB_C_2.0; USB_C_XKB_U262-16XN-4BVC11
U13, U14: PCT2075; PCT2075TP_147
U15, U16: XT90PW-M; AMASS_XT90PW-M_Horizontal
U17, U18, U19, U20, U21, U22, U23, U24, U25: XT30_V; AMASS_XT30U-F_1x02_P5.0mm_Vertical
U26, U32, U33, U35, U36, U37, U38, U39: ESC_CONN; 5x3.5x2mm_smd_pad
U34: AP2213-8_SOIC; SOIC-8_3.9x4.9mm_P1.27mm
U42: SOIC-8_3.9x4.9mm_P1.27mm

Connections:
3-3V_1: C15.2, C29.2, F1.2, R32.1, R38.1, R39.1, R40.1, R48.2, U4.9 (OUT), U13.8 (VCC)
3-3V_2: C16.2, F2.2, R34.1, R41.1, R42.1, R43.1, U5.9 (OUT)
3-3V_3: C22.2, F3.2, R16.1, R36.1, R58.1, R59.1, U6.9 (OUT)
5V_1: C42.2, C46.2, C50.2, F4.2, JP1.3, JP2.3, L1.2, R44.1, R45.1, R51.1, R66.1, R72.2
5V_2: C6.2, C44.2, C48.2, F5.2, L2.2, R46.1, R47.1, R71.1, R76.2
5V_3: C47.2, C49.2, C51.2, F6.2, L3.2, R60.1, R61.1, R75.1, R78.2
12V_1: C20.2, C21.2, C26.2, F7.2, L4.2, R68.2, R86.1, R89.2
12V_2: C52.2, C56.2, C57.2, F8.2, L5.2, R69.2, R87.1, R91.2
12V_3: C58.2, C74.2, C75.2, F9.2, L6.2, R70.2, R88.1, R93.2
+3V3: C1.2, C3.2, C7.2, C9.2, C10.2, C14.2, C17.2, C30.2, C80.2, C81.2, IC1.3 (~WP_(IO2)), IC1.7 (~HOLD_(IO3)), IC1.8 (VCC), IC2.6 (VDDANA), IC2.17 (VDDIO_1), IC2.36 (VDDIO_2), IC2.44 (VDDIN), J5.2, J6.2, J7.4 (VDD), JP1.1, JP2.1, R1.1, R53.2, R96.2, R97.2, R98.2, U1.1 (Vref), U2.1 (VCC), U3.1 (VCC), U14.8 (VCC), U34.3 (VOUT), U42.8 (V+)
+BATT: C5.1, C11.1, C12.1, C13.1, C18.1, C19.1, C24.1, C53.1, C54.1, C55.1, Q3.1 (S), Q4.1 (S), Q5.1 (S), Q6.1 (S), Q9.1 (S), Q10.1 (S), Q11.1 (S), Q12.1 (S), R15.1, R29.1, R30.1, R31.1, U4.16 (IN), U5.16 (IN), U6.16 (IN), U9.5 (IN), U9.6 (IN), U9.7 (IN), U9.9 (IN), U9.10 (EN/UVLO), U11.5 (IN), U11.6 (IN), U11.7 (IN), U11.9 (IN), U11.10 (EN/UVLO), U12.5 (IN), U12.6 (IN), U12.7 (IN), U12.9 (IN), U12.10 (EN/UVLO), U26.2 (+), U29.5 (IN), U29.6 (IN), U29.7 (IN), U29.9 (IN), U29.10 (EN/UVLO), U30.5 (IN), U30.6 (IN), U30.7 (IN), U30.9 (IN), U30.10 (EN/UVLO), U31.5 (IN), U31.6 (IN), U31.7 (IN), U31.9 (IN), U31.10 (EN/UVLO), U32.2 (+), U33.2 (+), U35.2 (+), U36.2 (+), U37.2 (+), U38.2 (+), U39.2 (+)
/A0_SENSE: IC2.3 (PA02), J4.3, TP7.1
/A5_SENSE: IC2.47 (PB02), J3.3, TP15.1
/BUZZER: IC2.25 (PA16), R49.2, R63.2
/MISO: IC2.21 (PA12), J7.7 (DOUT), TP9.1
/MOSI: IC2.19 (PB10), J7.3 (DIN), TP5.1
/SCK: IC2.20 (PB11), J7.5 (SCLK), TP6.1
/SCL: IC2.32 (PA23), J5.4, J6.4, R98.1, U13.2 (SCL), U14.2 (SCL)
/SDA: IC2.31 (PA22), J5.3, J6.3, R97.1, U13.1 (SDA), U14.1 (SDA)
/SD_CS: IC2.23 (PA14), J7.2 (CS), TP10.1
/SERIAL1_RX: IC2.16 (PA11), J1.3
/SERIAL1_TX: IC2.15 (PA10), J1.2
/SWCLK: IC2.45 (PA30), U1.4 (SWDCLK/TCK)
/SWDIO: IC2.46 (PA31), U1.2 (SWDIO/TMS)
/USB_D+: IC2.34 (PA25), U10.A6 (D+), U10.B6 (D+)
/USB_D-: IC2.33 (PA24), U10.A7 (D-), U10.B7 (D-)
/batt_ctl/BATT_1_CTL: IC2.27 (PA18), R6.2, R25.2, TP11.1
/batt_ctl/BATT_1_CURR: IC2.8 (PB09), R7.1, TP4.1
/batt_ctl/BATT_1_INT: IC2.4 (PA03), TP21.1, U42.1 (A)
/batt_ctl/BATT_1_VSENSE: IC2.7 (PB08), R17.2, R18.1, TP3.1
/batt_ctl/BATT_2_CTL: IC2.26 (PA17), R23.2, R62.1, TP14.1
/batt_ctl/BATT_2_CURR: IC2.9 (PA04), R24.1, TP12.1
/batt_ctl/BATT_2_INT: IC2.12 (PA07), TP22.1, U42.7 (B)
/batt_ctl/BATT_2_VSENSE: IC2.10 (PA05), R19.2, R20.1, TP8.1
/processor/FLASH_CS: IC1.1 (~CS), IC2.39 (PA27), R1.2
/processor/FLASH_MISO: IC1.2 (SO_(IO1)), IC2.48 (PB03)
/processor/FLASH_MOSI: IC1.5 (SI_(IO0)), IC2.37 (PB22)
/processor/FLASH_SCK: IC1.6 (SCLK), IC2.38 (PB23)
/~RESET_RAW: IC2.40 (~RESET), J1.1, SW1.1, TP1.1, U1.10 (~RESET)
BATT_1_PWR: D2.2 (A), R5.1, R17.1, R27.2, TP17.1, U2.6 (IP-), U15.2 (+)
BATT_2_PWR: D12.2 (A), R9.1, R11.2, R19.1, TP18.1, U3.6 (IP-), U16.2 (+)
GND: C5.2, C6.1, C11.2, C12.2, C13.2, C15.1, C16.1, C18.2, C19.2, C20.1, C21.1, C22.1, C23.2, C24.2, C25.2, C26.1, C27.2, C28.2, C29.1, C31.2, C32.1, C35.1, C36.2, C41.1, C42.1, C44.1, C46.1, C47.1, C48.1, C49.1, C50.1, C51.1, C52.1, C53.2, C54.2, C55.2, C56.1, C57.1, C58.1, C59.2, C60.2, C61.2, C62.2, C63.2, C64.2, C65.1, C66.1, C67.1, C74.1, C75.1, D3.1 (K), D4.1 (K), D5.1 (K), D6.1 (K), D7.1 (K), D8.1 (K), D9.1 (K), D10.1 (K), D11.1 (K), D14.1 (K), D15.1 (K), D16.1 (K), NT1.2, R3.2, R33.2, R35.2, R37.2, R52.2, R73.2, R74.1, R77.1, R79.1, R81.2, R83.2, R85.2, R90.2, R92.2, R94.2, TP16.1, TP19.1, TP20.1, U4.3 (AGND), U4.12 (PGND), U4.13 (PGND), U4.14 (PGND), U5.3 (AGND), U5.12 (PGND), U5.13 (PGND), U5.14 (PGND), U6.3 (AGND), U6.12 (PGND), U6.13 (PGND), U6.14 (PGND), U9.2 (PGND), U9.3 (PGND), U9.11 (PGND), U9.21 (SGND), U9.25 (EP), U11.2 (PGND), U11.3 (PGND), U11.11 (PGND), U11.21 (SGND), U11.25 (EP), U12.2 (PGND), U12.3 (PGND), U12.11 (PGND), U12.21 (SGND), U12.25 (EP), U13.4 (GND), U13.9 (EP_GND), U15.1 (-), U16.1 (-), U17.1 (-), U18.1 (-), U19.1 (-), U20.1 (-), U21.1 (-), U22.1 (-), U23.1 (-), U24.1 (-), U25.1 (-), U26.1 (-), U29.2 (PGND), U29.3 (PGND), U29.11 (PGND), U29.21 (SGND), U29.25 (EP), U30.2 (PGND), U30.3 (PGND), U30.11 (PGND), U30.21 (SGND), U30.25 (EP), U31.2 (PGND), U31.3 (PGND), U31.11 (PGND), U31.21 (SGND), U31.25 (EP), U32.1 (-), U33.1 (-), U35.1 (-), U36.1 (-), U37.1 (-), U38.1 (-), U39.1 (-)
GNDD: C1.1, C2.2, C3.1, C4.1, C7.1, C8.1, C9.1, C10.1, C14.1, C17.1, C30.1, C33.1, C34.2, C80.1, C81.1, IC1.4 (VSS), IC2.5 (GNDANA), IC2.18 (GND_1), IC2.35 (GND_2), IC2.42 (GND_3), IC2.49 (EP_GND), J1.4, J3.2, J4.2, J5.1, J6.1, J7.6 (GND), NT1.1, Q1.2 (S), Q2.2 (S), Q7.2 (S), R6.1, R8.1, R10.2, R18.2, R20.2, R23.1, R26.2, R49.1, R50.2, R99.2, SW1.3, TP13.1, U1.3 (GND), U1.5 (GND), U2.2 (GND), U3.2 (GND), U10.A1 (GND), U10.A12 (GND), U10.B1 (GND), U10.B12 (GND), U10.S1 (SHIELD), U14.4 (GND), U14.5 (A2), U14.6 (A1), U14.7 (A0), U14.9 (EP_GND), U34.5 (GND), U34.6 (GND), U34.7 (GND), U34.8 (GND), U42.4 (V-)
unnamed: C2.1, IC2.43 (VDDCORE)
unnamed: C41.2, R75.2, U12.20 (EXTVCC)
unnamed: C33.2, D1.1 (K), D2.1 (K), D12.1 (K), U34.1 (EN), U34.2 (VIN)
unnamed: C66.2, R87.2, U30.20 (EXTVCC)
unnamed: C65.2, R86.2, U29.20 (EXTVCC)
unnamed: C67.2, R88.2, U31.20 (EXTVCC)
unnamed: C32.2, R66.2, U9.20 (EXTVCC)
unnamed: C35.2, R71.2, U11.20 (EXTVCC)
unnamed: C37.1, L1.1, U9.1 (LX), U9.23 (LX), U9.24 (LX)
unnamed: C38.1, L2.1, U11.1 (LX), U11.23 (LX), U11.24 (LX)
unnamed: C43.1, L3.1, U12.1 (LX), U12.23 (LX), U12.24 (LX)
unnamed: C68.1, L4.1, U29.1 (LX), U29.23 (LX), U29.24 (LX)
unnamed: C69.1, L5.1, U30.1 (LX), U30.23 (LX), U30.24 (LX)
unnamed: C72.1, L6.1, U31.1 (LX), U31.23 (LX), U31.24 (LX)
unnamed: D3.2 (A), R5.2
unnamed: D4.2 (A), R9.2
unnamed: D5.2 (A), R15.2
unnamed: D6.2 (A), R16.2, R58.2, R59.2
unnamed: D7.2 (A), R38.2, R39.2, R40.2
unnamed: D8.2 (A), R41.2, R42.2, R43.2
unnamed: D9.2 (A), R44.2, R45.2
unnamed: D10.2 (A), R46.2, R47.2
unnamed: D11.2 (A), R60.2, R61.2
unnamed: D14.2 (A), R68.1
unnamed: D15.2 (A), R69.1
unnamed: D16.2 (A), R70.1
unnamed: J3.1, JP1.2
unnamed: J4.1, JP2.2
unnamed: Q1.3 (D), R12.1, R13.2, R14.2, R21.2, R22.2
unnamed: Q1.1 (G), R25.1
unnamed: Q2.3 (D), R28.1, R54.2, R55.2, R56.2, R57.2
unnamed: Q2.1 (G), R62.2
unnamed: Q3.3 (D), Q4.3 (D), Q5.3 (D), Q6.3 (D), R12.2, U2.5 (IP+)
unnamed: Q3.2 (G), R13.1
unnamed: Q4.2 (G), R14.1
unnamed: Q5.2 (G), R21.1
unnamed: Q6.2 (G), R22.1
unnamed: Q7.3 (D), SP1.2 (-)
unnamed: Q7.1 (G), R63.1
unnamed: Q9.2 (G), R54.1
unnamed: Q9.3 (D), Q10.3 (D), Q11.3 (D), Q12.3 (D), R28.2, U3.5 (IP+)
unnamed: Q10.2 (G), R55.1
unnamed: Q11.2 (G), R56.1
unnamed: Q12.2 (G), R57.1
unnamed: R51.2, SP1.1 (+)
unnamed: TP2.1, U1.9 (GNDDetect)
unnamed: C4.2, R7.2, U2.3 (VOUT)
unnamed: C8.2, R24.2, U3.3 (VOUT)
unnamed: R29.2, U4.17 (EN)
unnamed: R32.2, R33.1, U4.1 (FB)
unnamed: R30.2, U5.17 (EN)
unnamed: R34.2, R35.1, U5.1 (FB)
unnamed: R31.2, U6.17 (EN)
unnamed: R36.2, R37.1, U6.1 (FB)
unnamed: C37.2, U9.22 (BST)
unnamed: C39.2, U9.17 (CF)
unnamed: C39.1, R72.1, R74.2, U9.18 (FB)
unnamed: R3.1, U9.19 (RT)
unnamed: C27.1, U9.16 (SS)
unnamed: C23.1, R2.2, U9.12 (VCC)
unnamed: R2.1, U9.14 (~RESET)
unnamed: R10.1, U10.A5 (CC1)
unnamed: R8.2, U10.B5 (CC2)
unnamed: C38.2, U11.22 (BST)
unnamed: C40.2, U11.17 (CF)
unnamed: C40.1, R76.1, R77.2, U11.18 (FB)
unnamed: R52.1, U11.19 (RT)
unnamed: C31.1, U11.16 (SS)
unnamed: C25.1, R4.2, U11.12 (VCC)
unnamed: R4.1, U11.14 (~RESET)
unnamed: C43.2, U12.22 (BST)
unnamed: C45.2, U12.17 (CF)
unnamed: C45.1, R78.1, R79.2, U12.18 (FB)
unnamed: R73.1, U12.19 (RT)
unnamed: C36.1, U12.16 (SS)
unnamed: C28.1, R67.2, U12.12 (VCC)
unnamed: R67.1, U12.14 (~RESET)
unnamed: R48.1, U13.3 (OS)
unnamed: R53.1, U14.3 (OS)
unnamed: F1.1, U17.2 (+)
unnamed: F2.1, U18.2 (+)
unnamed: F3.1, U19.2 (+)
unnamed: F4.1, U20.2 (+)
unnamed: F5.1, U21.2 (+)
unnamed: F6.1, U22.2 (+)
unnamed: F7.1, U23.2 (+)
unnamed: F8.1, U24.2 (+)
unnamed: F9.1, U25.2 (+)
unnamed: C68.2, U29.22 (BST)
unnamed: C71.2, U29.17 (CF)
unnamed: C71.1, R89.1, R90.1, U29.18 (FB)
unnamed: R81.1, U29.19 (RT)
unnamed: C62.1, U29.16 (SS)
unnamed: C59.1, R80.2, U29.12 (VCC)
unnamed: R80.1, U29.14 (~RESET)
unnamed: C69.2, U30.22 (BST)
unnamed: C70.2, U30.17 (CF)
unnamed: C70.1, R91.1, R92.1, U30.18 (FB)
unnamed: R83.1, U30.19 (RT)
unnamed: C63.1, U30.16 (SS)
unnamed: C60.1, R82.2, U30.12 (VCC)
unnamed: R82.1, U30.14 (~RESET)
unnamed: C72.2, U31.22 (BST)
unnamed: C73.2, U31.17 (CF)
unnamed: C73.1, R93.1, R94.1, U31.18 (FB)
unnamed: R85.1, U31.19 (RT)
unnamed: C64.1, U31.16 (SS)
unnamed: C61.1, R84.2, U31.12 (VCC)
unnamed: R84.1, U31.14 (~RESET)
unnamed: C34.1, U34.4 (BYP)
unnamed: R27.1, R50.1, U42.3 (A+)
unnamed: R96.1, R99.1, U42.2 (A-), U42.6 (B-)
unnamed: R11.1, R26.1, U42.5 (B+)
VUSB: D1.2 (A), U10.A4 (VBUS), U10.A9 (VBUS), U10.B4 (VBUS), U10.B9 (VBUS)

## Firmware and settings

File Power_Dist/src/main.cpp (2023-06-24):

#include <Arduino.h>

#include <SPI.h>
#include <SD.h>

#include <Adafruit_PCT2075.h>

#include <BuzzerTimer.h>

#define ALLOW_SERIAL_HLC_REPORT
#define ALLOW_SERIAL_DEBUG

// Pin Definitions
#define BATT_1_VSENSE A1
#define BATT_1_CURR 2
#define BATT_1_INT 4
#define BATT_1_CTL 10

#define BATT_2_VSENSE A4
#define BATT_2_CURR A3
#define BATT_2_INT 9
#define BATT_2_CTL 13

#define A0_SENSE A0
#define A5_SENSE A5
#define BUZZER 11
#define SD_CS 2
#define SERIAL_1_RX 0
#define SERIAL_1_TX 1

// Other stuff
#define BATT_EMPTY 14 // Empty voltage
#define MAX_TEMP 60 // Temperature at which an error is logged in C

File file;
String buffer;

#define SD_UPDATE_INTERVAL  1000000
unsigned long sdPrevUpdate;

#define HLC_REPORT_INTERVAL 5000000
unsigned long hlcReportPrevUpdate;

volatile bool batt1On;
volatile bool batt2On;
bool batt1Installed;
bool batt2Installed;
float batt1V;
float batt2V;
float batt1Curr;
float batt2Curr;
#define CURR_SENSE_INTERVAL     1000000
#define CURR_SENSE_VOLTAGE_MULT 11
#define CURR_SENSE_CURR_MULT    37.8788
#define CURR_SENSE_VOLT_OFFSET  0
#define CURR_SENSE_CURR_OFFSET  0.330
unsigned long prevCurrSense;
float batt1VFIFO[10];
float batt2VFIFO[10];


#define HIGH_CURRENT    50 //Amps
bool batt1CurrErrorFlag;
bool batt2CurrErrorFlag;
bool dualLowErrorFlag;


#define SWITCHING_GRACE 1000000 // isr trigger grace period in micros
volatile bool ISR_Override;
volatile unsigned long prevSwitchTime;


// Kill switch = arming switch
#define KILL_SWITCH_GRACE   500000
unsigned long armingTimer; 
bool armingWaiting;
bool armedWaitingState;
bool armed;


Adafruit_PCT2075 MCTherm;
Adafruit_PCT2075 RegTherm;
bool MCThermErrorFlag;
bool RegThermErrorFlag;

// Buzzer stuff
bool buzzOn;
unsigned long prevBuzz;
#define BUZZ_INTERVAL_RAPID   100000
#define BUZZ_INTERVAL_SLOW    200000
#define BUZZ_FULL             1
#define BUZZ_OFF              0

BuzzerTimer buzzerTimer;

float getPinVolt(uint8_t pin);
float calcVBatt(float vsense);
void batt1ISR();
void batt2ISR();
void pollBatteries();
bool inSwitchingTimeout();
float getBatt1Curr();
float getBatt2Curr();
void hlcReport();

void setup() {
  Serial.begin(112500);
  // while (!Serial) {
  //   ;
  // }

  pinMode(BATT_1_VSENSE, INPUT_PULLDOWN);
  pinMode(BATT_1_CURR, INPUT_PULLDOWN);
  pinMode(BATT_1_INT, INPUT_PULLUP);
  pinMode(BATT_1_CTL, OUTPUT);

  pinMode(BATT_2_VSENSE, INPUT_PULLDOWN);
  pinMode(BATT_2_CURR, INPUT_PULLDOWN);
  pinMode(BATT_2_INT, INPUT_PULLUP);
  pinMode(BATT_2_CTL, OUTPUT);

  pinMode(A0_SENSE, INPUT);
  pinMode(A5_SENSE, INPUT);
  pinMode(SERIAL_1_RX, INPUT_PULLUP);

  // attachInterrupt(digitalPinToInterrupt(BATT_1_INT), batt1ISR, FALLING);
  // attachInterrupt(digitalPinToInterrupt(BATT_2_INT), batt2ISR, FALLING);

  batt1On = false;
  batt2On = false;
  pollBatteries();
  digitalWrite(BATT_1_CTL, LOW);
  digitalWrite(BATT_2_CTL, LOW);

#ifdef ALLOW_SERIAL_DEBUG
  Serial.println("Read Batt 1:" + String(batt1V));
  Serial.println("Read Batt 2:" + String(batt2V));
#endif

  batt1Curr = 0;
  batt2Curr = 0;
  prevCurrSense = micros();
  for (int x = 0; x < sizeof(batt1VFIFO) / sizeof(float); x++) {
    batt1VFIFO[x] = getPinVolt(BATT_1_CURR);
    batt2VFIFO[x] = getPinVolt(BATT_2_CURR);
  }


  buffer = "";

  // Not equal to because there is a possibility that neither battery is actually plugged in (just mcu)
  // if (batt1V > batt2V) {
  //   digitalWrite(BATT_1_CTL, HIGH);
  //   batt1On = true;
  //   Serial.println("Selected batt 1!");
  //   buffer += "Selected batt 1 at init";
  // }
  // else {
  //   digitalWrite(BATT_2_CTL, HIGH);
  //   batt2On = true;
  //   Serial.println("Selected batt 2!");
  //   buffer += "Selected batt 2 at init";
  // }

  prevSwitchTime = micros();
  ISR_Override = false;

  armingWaiting = false;
  armingTimer = micros();
  armed = false;
  armedWaitingState = false;

  batt1CurrErrorFlag = false;
  batt2CurrErrorFlag = false;
  dualLowErrorFlag = false;

  MCThermErrorFlag = false;
  RegThermErrorFlag = false;
  buzzOn = true;
  prevBuzz = micros();

  sdPrevUpdate = micros();
  hlcReportPrevUpdate = micros();
  

  if (!SD.begin(SD_CS)) {
#ifdef ALLOW_SERIAL_DEBUG
    Serial.println("Connection to SD Card failed");
#endif
  }
  if (SD.exists("log.txt"))
    SD.remove("log.txt");
  file = SD.open("log.txt", FILE_WRITE);
  
  file.println("Onyx Unified PDB #2");

  // Initialize Thermometers
  if (!MCTherm.begin(0x48, &Wire)) {
    file.println("MCTherm init failed");
  }
  if (!RegTherm.begin(0x37, &Wire))
    file.println("RegTherm init failed");

  buzzerTimer.set(BUZZ_INTERVAL_SLOW, 4);
  file.flush();

  Serial.println("Hello");
}

void loop() {

  pollBatteries();

#ifdef ALLOW_SERIAL_HLC_REPORT
  hlcReport();
#endif

  // Handle the kill switch / arming and disarming

  // if (((!digitalRead(SERIAL_1_RX) && armed) || (digitalRead(SERIAL_1_RX) && !armed)) && !armingWaiting) {
  //   armingWaiting = true;
  //   armedWaitingState = digitalRead(SERIAL_1_RX);
  //   armingTimer = micros();
  // }

  // if (armingWaiting && (micros() - armingTimer) > KILL_SWITCH_GRACE) {
  //   armingWaiting = false;
  //   armingTimer = micros();
  //   if (digitalRead(SERIAL_1_RX) == armedWaitingState) {
  //     armed = !armed;
  //     if (!armed) {
  //       buffer += "Disarmed";
  //       Serial.println("Disarmed");
  //     }
  //     else if (armed) {
  //       buffer += "armed";
  //       Serial.println("Armed");
  //     }
  //   }
  // }


  if ((micros() - armingTimer) > KILL_SWITCH_GRACE) {
    armed = digitalRead(SERIAL_1_RX);
    armingTimer = micros();
  }

  if (!armed) {
    digitalWrite(BATT_1_CTL, LOW);
    batt1On = false;
    digitalWrite(BATT_2_CTL, LOW);
    batt2On = false;  
  }

  if (!inSwitchingTimeout() && armed) {

    // In the case that both batteries dropped low and then one was replaced
    if (batt1On && batt2On) {
      if (batt1V > BATT_EMPTY) {
        digitalWrite(BATT_2_CTL, LOW);
        batt2On = false;
        prevSwitchTime = micros();
#ifdef ALLOW_SERIAL_DEBUG
        Serial.println("Selected Batt 1!");
#endif
        buffer += "Batt 1 was reinstalled charged; switching there";
      }
      if (batt2V > BATT_EMPTY) {
        digitalWrite(BATT_1_CTL, LOW);
        batt1On = false;
        prevSwitchTime = micros();
#ifdef ALLOW_SERIAL_DEBUG
        Serial.println("Selected Batt 2!");
#endif
        buffer += "Batt 2 was reinstalled charged; switching there";
      }
    }

    // In the case that both batteries were off (disarmed)
    if (!batt1On && !batt2On) {
      if (batt1V > batt2V) {
        digitalWrite(BATT_1_CTL, HIGH);
        batt1On = true;
        buffer += "Selected batt 1 after disarm";
      }
      else {
        digitalWrite(BATT_2_CTL, HIGH);
        batt2On = true;
        buffer += "Selected batt 2 after disarm";
      }
    }

    if (batt1On && batt1V < BATT_EMPTY && batt2Installed && !batt2On) {
      ISR_Override = true;
      digitalWrite(BATT_2_CTL, HIGH);
      batt2On = true;
      prevSwitchTime = micros();
#ifdef ALLOW_SERIAL_DEBUG
      Serial.println("Switched to batt 2!");
#endif
      buffer += "Switching to batt 2";
      if (batt2V > BATT_EMPTY) {
        digitalWrite(BATT_1_CTL, LOW);
        batt1On = false;
        prevSwitchTime = micros();
        buzzerTimer.set(BUZZ_INTERVAL_SLOW, 4);
      }
      else {
        buzzerTimer.set(BUZZ_INTERVAL_RAPID, 20);
      }
      ISR_Override = false;
    }
    if (batt2On && batt2V < BATT_EMPTY && batt1Installed && !batt1On) {
      ISR_Override = true;
      digitalWrite(BATT_1_CTL, HIGH);
      batt1On = true;
      prevSwitchTime = micros();
#ifdef ALLOW_SERIAL_DEBUG
      Serial.println("Switched to batt 1!");
#endif
      buffer += "Switching to batt 1";
      if (batt1V > BATT_EMPTY) {
        digitalWrite(BATT_2_CTL, LOW);
        batt2On = false;
        prevSwitchTime = micros();
        buzzerTimer.set(BUZZ_INTERVAL_SLOW, 4);
      }
      else {
        buzzerTimer.set(BUZZ_INTERVAL_RAPID, 20);
      }
      ISR_Override = false;
    }

  }

  // Errors
  if (batt1Installed && batt1V < BATT_EMPTY && batt2Installed && batt2V < BATT_EMPTY) {
    if (!dualLowErrorFlag) {
      buffer += "Both batteries empty";
      dualLowErrorFlag = true;
    }
  }
  else {
    dualLowErrorFlag = false;
  }


  // Temperature
  if (MCTherm.getTemperature() > MAX_TEMP) {
    if (!MCThermErrorFlag) {
      buffer += "MC Thermometer logged: " + (String)MCTherm.getTemperature();
      MCThermErrorFlag = true;
      buzzerTimer.set(BUZZ_INTERVAL_RAPID, 20);
    }
  }
  else {
    MCThermErrorFlag = false;
  }

  if (RegTherm.getTemperature() > MAX_TEMP) {
    if (!RegThermErrorFlag) {
      buffer += "Reg Thermometer logged: " + (String)RegTherm.getTemperature();
      RegThermErrorFlag = true;
      buzzerTimer.set(BUZZ_INTERVAL_RAPID, 20);
    }
  }
  else {
    RegThermErrorFlag = false;
  }


  // Current
  if (batt1Curr > HIGH_CURRENT) {
    if (!batt1CurrErrorFlag) {
      buffer += "Batt 1 current: " + (String)batt1Curr;
      batt1CurrErrorFlag = true;
      buzzerTimer.set(BUZZ_INTERVAL_RAPID, 20);
    }
  }
  else {
    batt1CurrErrorFlag = false;
  }
  if (batt2Curr > HIGH_CURRENT) {
    if (!batt2CurrErrorFlag) {
      buffer += "Batt 2 current: " + (String)batt2Curr;
      batt2CurrErrorFlag = true;
      buzzerTimer.set(BUZZ_INTERVAL_RAPID, 20);
    }
  }
  else {
    batt1CurrErrorFlag = false;
  }


  if (buzzerTimer.timeUp()) {
    digitalWrite(BUZZER, buzzOn);
    buzzOn = !buzzOn;
  }


  if (micros() - sdPrevUpdate > SD_UPDATE_INTERVAL) {
    if (buffer.length() > 0) {
      file.println(buffer);
      file.flush();
      buffer.remove(0);
    }
    sdPrevUpdate = micros();
  }

}

// void batt1ISR() {
//   if (batt2Installed && !inSwitchingTimeout() && !ISR_Override) {
//     digitalWrite(BATT_2_CTL, HIGH);
//     digitalWrite(BATT_1_CTL, LOW);
//     batt2On = true;
//     prevSwitchTime = micros();
//     Serial.println("Batt 1 removed, switched to 2");
//   }
//   else {
//     // fuck
//     file.println("Batt 1 disconnect while Batt2 uninstalled");
//   }
// }

// void batt2ISR() {
//   if (batt1Installed && !inSwitchingTimeout() && !ISR_Override) {
//     digitalWrite(BATT_1_CTL, HIGH);
//     digitalWrite(BATT_2_CTL, LOW);
//     batt1On = true;
//     prevSwitchTime = micros();
//     Serial.println("Batt 2 removed, switched to 1");
//   }
//   else {
//     // fuck
//     file.println("Batt 2 disconnect while Batt1 uninstalled");
//   }
// }

float getPinVolt(uint8_t pin) {
  return (analogRead(pin) * 3.3) / 1048;
}

// Calculates the vsense pin voltage to the battery voltage
float calcVBatt(float vsense) { 
  return vsense / (2.54 / 14.94);
}

void pollBatteries() {
  batt1V = calcVBatt(getPinVolt(BATT_1_VSENSE));
  batt2V = calcVBatt(getPinVolt(BATT_2_VSENSE));

  batt1Installed = batt1V > 0.5;
  batt2Installed = batt2V > 0.5;

  if (micros() - prevCurrSense > CURR_SENSE_INTERVAL) {

    uint8_t bufferLen = sizeof(batt1VFIFO) / sizeof(float);

    float batt1Sum = 0;
    float batt2Sum = 0;
    for (int x = bufferLen - 1; x > 0; x--) {
      batt1VFIFO[x] = batt1VFIFO[x - 1];
      batt2VFIFO[x] = batt2VFIFO[x - 1];
      batt1Sum += batt1VFIFO[x];
      batt2Sum += batt2VFIFO[x];
    }
    batt1VFIFO[0] = getPinVolt(BATT_1_CURR);
    batt2VFIFO[0] = getPinVolt(BATT_2_CURR);
    batt1Sum += batt1VFIFO[0];
    batt2Sum += batt2VFIFO[0];

    float batt1VAvg = batt1Sum / bufferLen;
    float batt2VAvg = batt2Sum / bufferLen;

    // TEST LATER
//     float test1Voltage = (batt1VAvg - CURR_SENSE_VOLT_OFFSET) * CURR_SENSE_VOLTAGE_MULT;
// #ifdef ALLOW_SERIAL_DEBUG
//     Serial.println("ACS measured V1: " + String(test1Voltage));
// #endif
//     float test2Voltage = (batt2VAvg - CURR_SENSE_VOLT_OFFSET) * CURR_SENSE_VOLTAGE_MULT;
// #ifdef ALLOW_SERIAL_DEBUG
//     Serial.println("ACS measured V1: " + String(test1Voltage));
// #endif

// refer to https://github.dev/ArduPilot/ardupilot ; /libraries/AP_BattMonitor/AP_BattMonitor_Analog.cpp for code implementation, and 
// https://github.com/mavlink/qgroundcontrol/blob/master/src/AutoPilotPlugins/APM/APMPowerComponent.qml for constants

    batt1Curr = (batt1VAvg - CURR_SENSE_CURR_OFFSET) * CURR_SENSE_CURR_MULT;
    batt2Curr = (batt2VAvg - CURR_SENSE_CURR_OFFSET) * CURR_SENSE_CURR_MULT;

    prevCurrSense = micros();
  }

}


bool inSwitchingTimeout() {
  return (micros() - prevSwitchTime) < SWITCHING_GRACE;
}

void hlcReport() {
  if (micros() - hlcReportPrevUpdate > HLC_REPORT_INTERVAL) {
    char report[100];
    sprintf(report, "[%lu,%d,%s,%s,%s,%s,%s,%s]", millis(), (int)armed, String(batt1V, 3).c_str(), String(batt1Curr, 3).c_str(), String(batt2V, 3).c_str(), String(batt2Curr, 3).c_str(), String(RegTherm.getTemperature(), 3).c_str(), String(MCTherm.getTemperature(), 3).c_str()); 
    Serial.write(report);
    memset(report, 0, sizeof(buffer));
    hlcReportPrevUpdate = micros();
  }
}

// float getBatt1Curr() {
//   return (((analogRead(BATT_1_CURR) / 1048) * 3.3) - 0.33) * 50;
// }

// float getBatt2Curr() {
//   return (((analogRead(BATT_2_CURR) / 1048) * 3.3) - 0.33) * 50;
// }

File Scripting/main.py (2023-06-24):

import serial
import serial.tools.list_ports

def establishPort(port=None):
  if port:
    pdb_port = port
  else:
    available_ports = list(serial.tools.list_ports.comports())
    for port in available_ports:
      if "ItsyBitsy M0 Express" in port.description:
        pdb_port = port.device
  
  return serial.Serial(port=pdb_port, baudrate=115200, timeout=1)


def getBattInfo(serial_device):

  if serial_device.in_waiting:
  
    output = serial_device.readline().decode('ascii').strip()
    incoming = output[output.rfind("[") + 1 : len(output) - 1].split(",")
    data = {"Timestamp" : incoming[0], "Armed" : incoming[1], "Batt1V" : incoming[2], "Batt1Curr" : incoming[3], "Batt2V" : incoming[4], "Batt2Curr" : incoming[5], "RegTherm" : incoming[6], "MCTherm" : incoming[7]}
    return data
  else :
    return None


def main():

  serial_device = establishPort()

  while True: 
    x = getBattInfo(serial_device)
    if x:
      print(x)


if __name__ == "__main__":
  main()

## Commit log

2023-05-14 switching working, adding interrupts
2023-05-14 added interrupts and buzzer, untested
    [main.cpp]
2023-05-17 loop switching working, errors untested
    [main.cpp]
2023-05-17 added gerbers
    [1.0-B_Cu.gbr, 1.0-B_Mask.gbr, 1.0-B_Paste.gbr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]
2023-05-17 timer testing
2023-06-14 current sense updates
2023-06-23 current constant updates
